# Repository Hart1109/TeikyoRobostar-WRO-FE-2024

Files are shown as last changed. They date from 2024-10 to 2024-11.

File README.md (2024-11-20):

Engineering materials「Teikyo University」
====

This repository contains engineering materials of a self-driven vehicle's model participating in the WRO Future Engineers competition in the season 2024.

---
## Member
* Ryota Kanda (Born on July 12 ,2005)
* Yusei Owa (Born on March 29 ,2006)
* Yuichi Hasuda (coach)
## Content

* `t-photos` contains 2 photos of the team (an official one and one funny photo with all team members)
* `v-photos` contains 6 photos of the vehicle (from every side, from top and bottom)
* `video` contains the video.md file with the link to a video where driving demonstration exists
* `schemes` contains one or several schematic diagrams in form of JPEG, PNG or PDF of the electromechanical components illustrating all the elements (electronic components and motors) used in the vehicle and how they connect to each other.
* `src` contains code of control software for all components which were programmed to participate in the competition
* `models` is for the files for models used by 3D printers, laser cutting machines and CNC machines to produce the vehicle elements.
* `other` is for other files which can be used to understand how to prepare the vehicle for the competition. It may include documentation how to connect to a SBC/SBM and upload files there, datasets, hardware specifications, communication protocols descriptions etc.

## Introduction
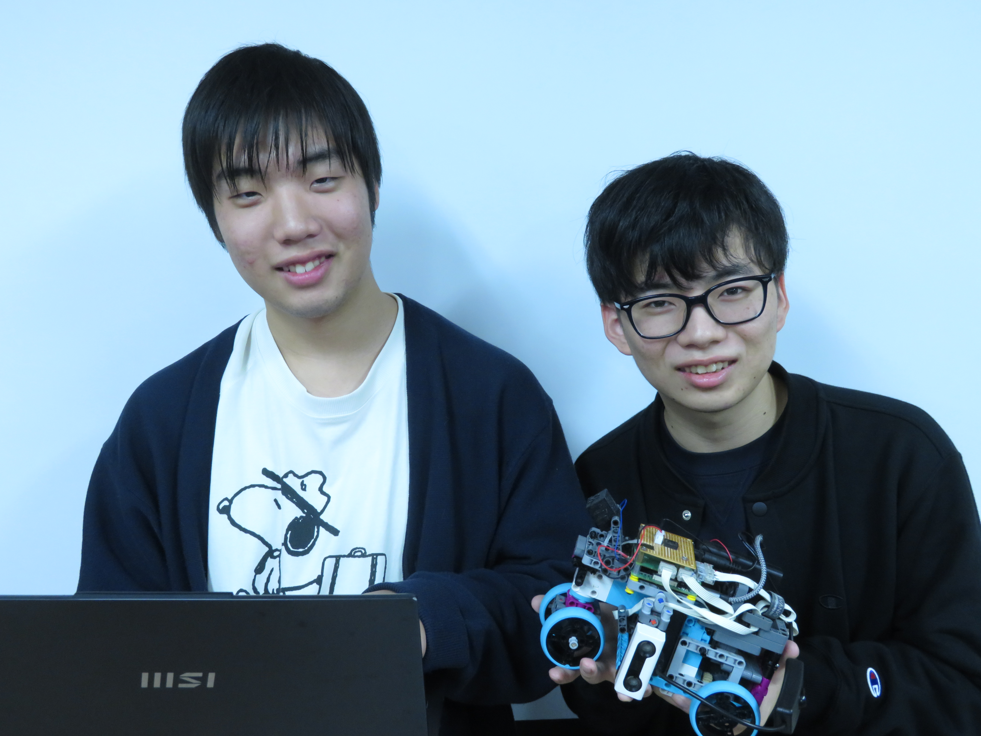
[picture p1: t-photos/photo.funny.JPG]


**Ryota Kanda:Robot design**・・・Left Side  
Ryota is a first-year student at Teikyo University and a member of the robotics club RoboLab. He is in charge of designing robots in the team and works hard practicing and designing every day. He is studying robot technology with the goal of becoming an engineer in the future. His hobbies are tea ceremony and origami.

**Yusei Owa**:Programmer・・・Right Side  
Yusei is a first-year student at Teikyo University and a member of the robotics club RoboLab. He is in charge of programming in the team. He uses the knowledge he learned in his university classes to design and improve programs. He is currently studying linux and python with the goal of becoming an engineer in the future. After school, he enjoys reading books.

---
Next, we describe the operation and programming environment of the freestanding robot.
First, download RealVNC Viewer from the following site
https://www.realvnc.com/en/connect/download/viewer/
 
 After downloading, find out the IP address of the machine and connect to it.

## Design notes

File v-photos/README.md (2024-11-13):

Vehicle's photos
====


↑Here is a picture of the back side.



↑Front side.



↑On the left.



↑Right side.



↑Bottom side.



↑Upper side.

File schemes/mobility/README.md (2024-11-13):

#  Mobility Management

## Motor Overview

### Selected motor
・SPIKE Prime L angular motor



### Specification of motor
・SPIKE Prime L angular motor
| part | performance |
| --- | --- |
| Output voltage | 5～9[V] |
| Rotation sensor  | one revolution:360count  |
| Wire  | 250mm |
| No Load |Torque: 0 Ncm <br> Speed: 175 RPM ± 15% <br> Current Consumption: 135 mA ± 15%|
| Maximum Efficiency | Torque: 8 Ncm <br> Speed: 135 RPM ± 15% <br> Current Consumption: 430 mA ± 15% |
| Stall | Torque: 25 Ncm <br> Speed: 0 RPM <br> Current Consumption: 1400 mA ± 15% |

### Reasons for choice
Easy to assemble and reassemble, making it suitable for fine-tuning of robots.In addition, the L motor for high output and high torque for both the front and rear wheels. It is a reliable and proven motor that was used by the winning team of tha WRO 2023 World Championships.

### Implementation Methods
The use of high-torque motors for the front and rear wheels is expected to shorten the competition time.

---
## Brief explanation of car body structure
The base of the robot is designed around the LEGO Education Spike Prime, and the robot is connected to a Raspberry Pi4, ultrasonic sensor, camera, cooling fan, and battery.In addition, the 3D model was used to fix the camera to prevent image distortion while the robot is running, and two ultrasonic sensors were installed on either side of the robot to keep it parallel to the wall at all times.

---
## Front wheel operation
Increasing the distance between the wheels of the vehicle has the advantage of making the steering more agile, allowing for fine angle adjustment and easier corner turning. For rough control of the wheels, the angle of the wheels is changed by turning the motor.




For a detailed explanation of the design, please click [here](https://github.com/Hart1109/TeikyoRobostar-WRO-FE-2024/blob/main/body%20information/Steering%20wheel%20assembly.pdf).

## Rear wheel operation

Differential gears are used for the rear wheel drive mechanism. The function of this component is to allow for the speed difference between the inner and outer wheels and distribute the output to both wheels, sending more power to the less loaded tire.



This mechanism enables smooth obstacle avoidance and cornering.

---

## 3Dmodels（camera mount）



This component is used to secure the Raspberry Pi Camera.

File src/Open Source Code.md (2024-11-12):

import cv2
import os
import numpy as np
import time
import threading
import RPi.GPIO as GPIO
GPIO.setmode(GPIO.BCM)
from buildhat import Motor, DistanceSensor, ColorSensor

motorBack = Motor('D')
motorFront = Motor('C')
distLeft = DistanceSensor('A', threshold_distance=100)
distRight = DistanceSensor('B', threshold_distance=100)
GPIO.setup(18, GPIO.IN, pull_up_down=GPIO.PUD_UP)

motorBack.stop()
motorFront.stop()

#Default setting
#Start speed
pw = -47
adjustment = 5

def setup():
    dist_L = distLeft.get_distance()#Stores distance to left wall
    dist_R = distRight.get_distance()#Stores distance to right wall
    motorFront.run_to_position(adjustment,blocking=False)
    print("standby")
    GPIO.wait_for_edge(18, GPIO.FALLING)
    time.sleep(0.3)
    
def setMotor():
    motorBack.set_default_speed(-pw)#Setting the motor speed of the rear wheels
    motorFront.set_default_speed(-pw)#Setting the motor speed of the front wheels

def run(pw):
    motorBack.start(pw)#Start speed setting

def stop():
    motorBack.stop()#Stops rear wheel movement
    motorFront.stop()#Stops front wheel movement

def runStraight():#Program to run horizontally against a wall
    if turnCount == 0:#When the direction is not set
        dif = dist_R - dist_L
        if (dif - firstDis < -10):
            motorFront.run_to_position(10,blocking=False)
            time.sleep(0.3)
        elif (dif - firstDis > 10):
            motorFront.run_to_position(-5,blocking=False)
            time.sleep(0.3)
    if rotation == "Left":#Counterclockwise rotation
        if dist_R < tDist - 10:
            motorFront.run_to_position(14,blocking=False)
            time.sleep(0.3)
        elif tDist - 10 <= dist_R and dist_R <= tDist + 10:
            motorFront.run_to_position(0,blocking=False)
            time.sleep(0.3)
        elif tDist + 10 < dist_R:
            motorFront.run_to_position(-6,blocking=False)
            time.sleep(0.3)
            
    if rotation == "Right":#Clockwise rotation
        if dist_L < tDist - 10:
            motorFront.run_to_position(-8,blocking=False)
            time.sleep(0.3)
        elif tDist - 10 <= dist_L and dist_L <= tDist + 10:
            motorFront.run_to_position(0,blocking=False)
            time.sleep(0.3)
        elif 250 <= dist_L:
            motorFront.run_to_position(14,blocking=False)
            time.sleep(0.3)
            
def backTurn():#Backward program
    if rotation == "Left":#Counterclockwise rotation
        motorFront.run_to_position(0,blocking=False)
        motorBack.run_for_degrees(360,-pw)
        motorFront.run_to_position(30, blocking=False)
        time.sleep(0.2)
        motorBack.run_for_degrees(50,pw)
        motorFront.run_to_position(30, blocking=False)
        time.sleep(0.2)
        motorBack.run_for_degrees(2050,pw)
        time.sleep(0.3)

    elif rotation == "Right":#Clockwise rotation
        motorFront.run_to_position(0,blocking=False)
        motorBack.run_for_degrees(360,-pw)
        motorFront.run_to_position(-30, blocking=False)
        time.sleep(0.2)
        motorBack.run_for_degrees(50,pw)
        motorFront.run_to_position(-30, blocking=False)
        time.sleep(0.2)
        motorBack.run_for_degrees(1800,pw)
        
def turn():#Turning the corner program
    if rotation == "Left":#Counterclockwise rotation
        motorFront.run_to_position(30, blocking=False)
        time.sleep(0.2)
        motorBack.run_for_degrees(50,pw)
        motorFront.run_to_position(30, blocking=False)
        time.sleep(0.2)
        motorBack.run_for_degrees(2050,pw)
        time.sleep(0.3)
        
    elif rotation == "Right":#Clockwise rotation
        motorFront.run_to_position(-30, blocking=False)
        time.sleep(0.2)
        motorBack.run_for_degrees(50,pw)
        motorFront.run_to_position(-30, blocking=False)
        time.sleep(0.2)
        motorBack.run_for_degrees(1800,pw)
      
#Enter initial values for each variable
x = 0
y = 0
finishCount = 0#Used during the finish section
allowRun = True#Determine if it is running or not.
turnCount = 0#Measure the number of times a corner is turned
rotation = ""
tDist = 0
turnWait = 0
backJudge = 200

#Mainprogram
setMotor()
setup()
while True:
    dist_L = distLeft.get_distance()#Stores distance to left wall
    dist_R = distRight.get_distance()#Stores distance to right wall
    
    if allowRun:
         run(pw)
    else:
        stop()
        break
    
    if x == 0:
        firstDis = dist_R - dist_L
        x += 1

    if rotation == "":
        runStraight()
        if dist_L < 0 or 1200 < dist_L:#If the left sensor cannot recognize the distance
            rotation = "Left"
        elif dist_R < 0 or 1200 < dist_R:#If the right sensor cannot recognize the distance
            rotation = "Right"
            
    if rotation == "Left":#Counterclockwise rotation
        if turnCount >= 12:#When you turned the corner 12 times
            if finishCount < 5:#If the count is 5 or more
                runStraight()
                finishCount += 1
            else:
                allowRun = False#If the count is less than 5
                print("stop")
                
        if (0 < dist_L and dist_L < 1200):#If the left sensor can recognize the distance
            turnWait = 0
            backJudge = dist_L
            runStraight()
            if y > 0:
                y -= 1
                
        if (dist_L < 0 or 1200 < dist_L):#If the left sensor cannot recognize the distance
            turnWait += 1
            if (y == 0) and turnWait == 2:
                print("turning")
                if backJudge < 120:#When the distance from the wall is close
                    turn()
                else:
                    backTurn()#When the distance from the wall is far
                tDist = distRight.get_distance()
                turnCount += 1
                y += 5
            else:
                runStraight()

    elif rotation == "Right":#Clockwise rotation
        if turnCount >= 12:#When you turned the corner 12 times
            if finishCount < 5:#If the count is 5 or more
                runStraight()
                finishCount += 1
            else:
                allowRun = False#If the count is less than 5
                print('stop')
                
        if (0 < dist_R and dist_R < 1200):#If the right sensor can recognize the distance
            turnWait = 0
            backJudge = dist_R
            runStraight()
            if y > 0:
                y -= 1

        if (dist_R < 0 or 1200 < dist_R):#If the right sensor cannot recognize the distance
            turnWait += 1
            if (y == 0) and turnWait == 2:
                print("turning")
                if backJudge < 120:#When the distance from the wall is close
                    turn()
                else:
                    backTurn()#When the distance from the wall is far
                tDist = distLeft.get_distance()
                turnCount += 1
                y += 5
            else:
                runStraight()
　　#Displays the value of each variable
    print(f"dL:{dist_L} dR:{dist_R} aR:{allowRun} tD:{tDist} ro:{rotation} count:{turnCount} y: {y} finish:{finishCount}")

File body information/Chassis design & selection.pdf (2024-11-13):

# Chassis design / selection

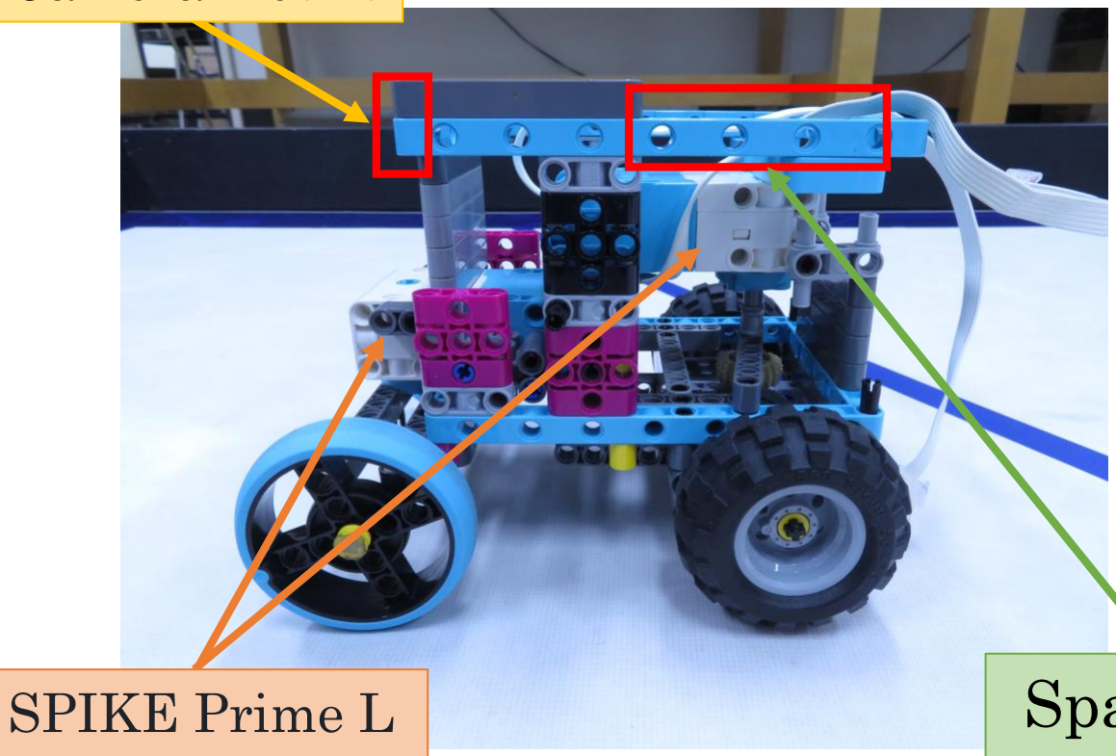
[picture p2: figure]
SPIKE Prime L

### Space for battery

Space is created at the rear of the vehicle to accommodate the mobile battery and battery box.

By creating a support with LEGO SPIKE, the parts were prevented from falling and the mounting performance was
improved.

angular motor

Camera mount

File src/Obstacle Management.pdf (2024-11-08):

# Souce code with detailed comments(1)

def setMotor():
motor.set_default_speed(100) motorS.set_default_speed(100)

def run(pw):
motor.start(pw)

def stop():
motor.stop()
motorS.stop()

## Necessary for robot

operation.forward, stop,

## etc.lograms

# Souce code with detailed comments(2)

def corner():
motorS.run_to_position(-15, blocking=False) time.sleep(0.2)
motor.run_for_degrees(300,-pw) motorS.run_to_position(15, blocking=False) time.sleep(0.2)
motor.run_for_degrees(100,pw) motorS.run_to_position(15, blocking=False) time.sleep(0.2)
motor.run_for_degrees(1000,pw)

def cornerB():
motorS.run_to_position(15, blocking=False) time.sleep(0.2)
motor.run_for_degrees(300,-pw) motorS.run_to_position(-15, blocking=False) time.sleep(0.2)
motor.run_for_degrees(100,pw) motorS.run_to_position(-15, blocking=False) time.sleep(0.2)
motor.run_for_degrees(1000,pw)

## 90-degree bend along an interior wallProgram for

# Souce code with detailed comments(3)

def correct_value(n):
if n < 150:
return 150
elif n > 450:
return 450
else:

setMotor()
cornerOn=False
x=0
segment_p = 0
dis = -1
count = 0
countB = 0
countC = 0
non = 0
CC = 0
CCC = 0

## Program to limit ultrasonic sensor values to a minimum of 150 and a maximum of 450

## Set initial values of variables necessary for executing the main program

while True:
if x == 0:
stop()
print('setup')
GPIO.wait_for_edge(18, GPIO.FALLING)

if rotation == “”:
runStraight()
if dist_L < 0 or 1200 < dist_L: rotation = “Left”
elif dist_R < 0 or 1200 < dist_R: rotation = “Right”

if shukai ==1:
dis_p = dist.get_distance()
else:
dis_p = distB.get_distance()

motorS.run_to_position(0, blocking=False) time.sleep(0.5)
run(pw)
x = 1

if count >=12:
CCC += 1
print (CCC)
if CCC == 100 :
stop()
break

## Main program Program to start the robot with a switch A program that counts the number of bends and stops the robot above a certain value

# Souce code with detailed comments(4)

# Souce code with detailed comments(5)

if shukai ==1:
dis = dist.get_distance()
else:
dis = distB.get_distance()

countB += 1
if dis == -1 or dis >1100 :
non += 1

if non >= 10 and countB >=180 or non > 15: if non > 10:
if shukai == 1:
cornerC()
else:
cornerD()
else:
if shukai == 1:
corner()
else:
cornerB()
if countB >= 120 or count == 0 and countB <= 119: count +=1

countC = 0
countB = 0
run(pw)

## Program measures distance to wall and moves forward while maintaining distance.When the distance becomes much larger than the measured value Or when it becomes unmeasurable,The

program turns 90 degrees.

# Souce code with detailed comments(6)

count +=1

countC = 0
countB = 0
run(pw)

while not 0 < dis < 340 and not countC > 60: if shukai == 1:
dis = dist.get_distance()
print(dis)
countC += 1
print(countC)
else:
dis = distB.get_distance() print(dis)
countC += 1
print(countC)

countC = 0
countD = 0

motorS.run_to_position(0, blocking=False) motor.run_for_degrees(100,pw)

## If the distance between the robot and the inner wall is too far after a 90-degree turn, program the robot to turn until a certain distance is

reached.

# Souce code with detailed comments(7)

if dis == -1:
if shukai == 1:
segment = 10
else:
segment = -10

elif dis <= 200:
if shukai == 1:
segment = -10
else:
segment = 10

elif dis <= 100:
if shukai == 1:
segment = -15
else:
segment = 15

## Program to change steering depending on distance from wall

elif dis >1000:
segment = 0

elif -10 <= dis_p - dis <= 25: segment = 0

elif 25 < dis_p - dis:
if shukai == 1:
segment = -5
else:
segment = 5

elif dis_p - dis < 30:
if shukai == 1:
segment = 10
else:
segment = -10

# Pseudo code

## Determine the color of the obstacle with the greatest width in the

camera's view.
↓

## When the width of the obstacle reaches the standard value, start

evasive action.
↓

## If the obstacle is red, avoid it to the right. If the obstacle is green, avoid it

to the left.

## Obstacle Challenge

# Frow diagrams

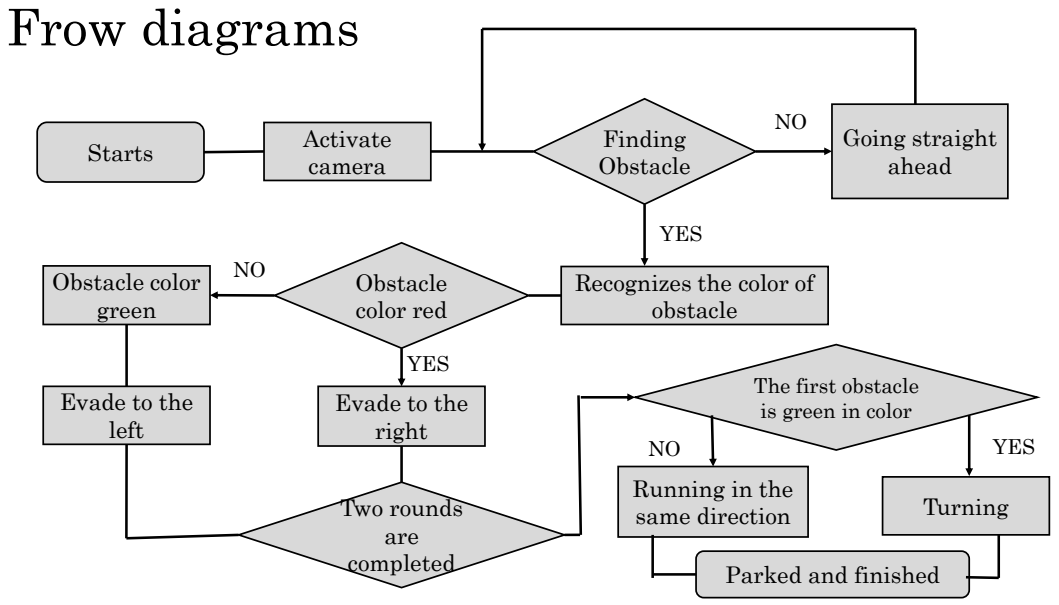
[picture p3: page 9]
Starts; Activate camera; Finding Obstacle; Going straight ahead; obstacle; Obstacle color red; Obstacle color green; Two rounds are completed; Turning; YES

Recognizes the color of

The first obstacle
is green in color

Evade to the
left

right

Running in the
same direction

Parked and finished

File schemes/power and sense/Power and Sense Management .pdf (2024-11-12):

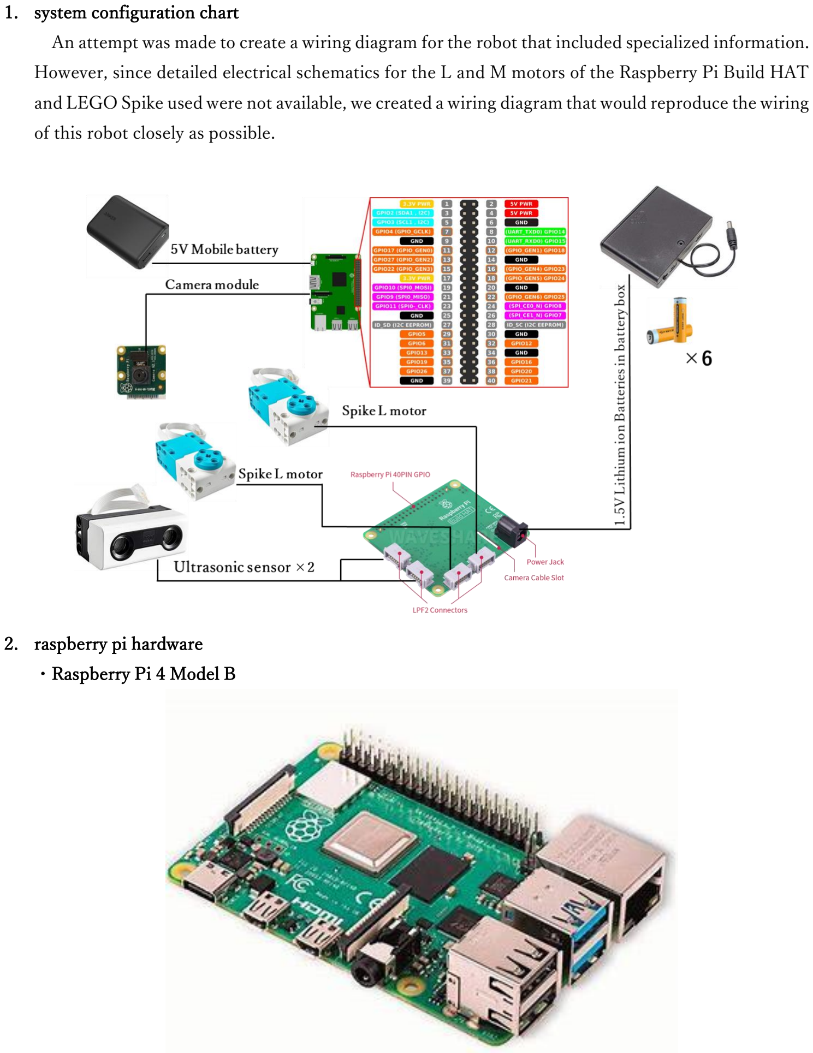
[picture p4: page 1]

1. system configuration chart
An attempt was made to create a wiring diagram for the robot that included specialized information. However, since detailed electrical schematics for the L and M motors of the Raspberry Pi Build HAT and LEGO Spike used were not available, we created a wiring diagram that would reproduce the wiring of this robot closely as possible.
2. raspberry pi hardware
・Raspberry Pi 4 Model B

(1) Product Information
part | Description
Processor | Broadcom BCM2711 Quad-Core Cortex-A72 (ARM v8) 64-bit SoC @ 1.5GHz
Memory | 8GB
Connectivity | 2.4GHz and 5.0GHz, IEEE 802.11b / g / n / ac wireless LAN, Bluetooth 5.0, BLE Gigabit Ethernet 2 x USB 3.0 ports 2 x USB 2.0 ports.
GPIO | Standard 40-pin GPIO header
Video sound | 2 x micro HDMI ports (supports up to 4Kp60) 2 lane MIPI DSI display port 2 lane MIPI CSI camera port 4-pole stereo audio and composite video port
Multimedia | H.265 (4Kp60 decoding); H.264 (1080p60 decoding, 1080p30 encoding) H.264 (1080p60 decode, 1080p30 encode) OpenGL ES, 3.0 graphics
SD card | Micro SD card slot for loading operating system and data storage
Input power | 5V DC (min. 3A1) via USB-C connector 5V DC via GPIO header (min. 3A1) Power over Ethernet (PoE) support (PoE HAT required separately)
(2) Reasons for choosing the Raspberry Pi 4 Model B
Lightweight and fast, it is the easiest single-board computer to use. It is highly flexible and can use a variety of sensors. It is also the most widely used single board computer by many people and is widely used in the field of electronic engineering, providing a wealth of information necessary for development.
(3) How to use the Raspberry Pi 4 Model B
The Raspberry Pi 4 is a small single board computer. It processes and analyzes images acquired from cameras in real time. The language used is Python and the opencv library is used for image processing.

・Raspberry Pi Build HAT

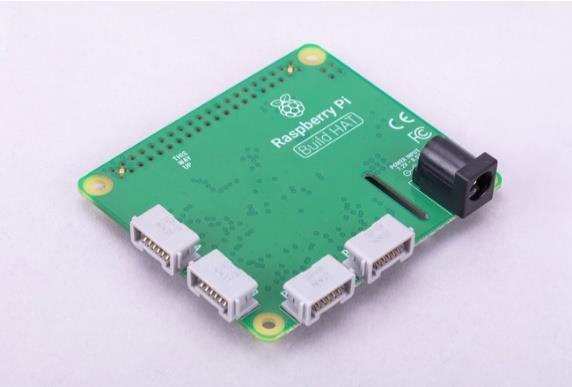
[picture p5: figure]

（１） Product Information
This product was used
https://www.switch-science.com/products/7565

（２） Reasons for choosing the Raspberry Pi Build HAT
The Raspberry Pi Build HAT can control up to four LEGO® Technic motors and sensors from a Raspberry Pi 4. The LEGO® Technic devices can be controlled by the easy-to-use Python libraries included in the LEGO® Education SPIKE Prime and SPIKE Prime Extension Sets.

（３） How to use the Raspberry Pi Build HAT
The Raspberry Pi Build HAT is not only used as an expansion port for angular motors and ultrasonic sensors, but also has the ability to step down a 9V power supply to 5V with its built-in switching regulator.
3. used battery
3-1 5V mobile battery

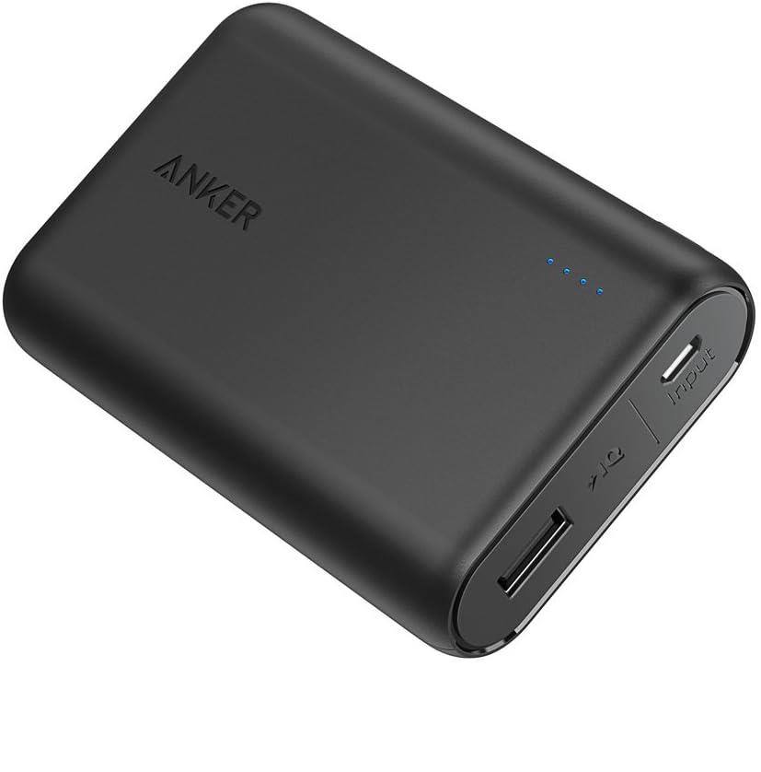
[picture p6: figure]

(1) Product Information
part | Description
capability | 10000mAh
manufacturer | Anker
Model number of the product | A1263
output | 5V = 2.4A
input | 5V = 2A
size | 92 x 60 x 22mm
weight | 180g
(2) Reason for selecting this part

To provide a stable power supply to the Raspberry Pi4. and 9V battery box is also used, which also

serves as a sub-battery. This allows the autonomous robot to operate for extended periods of time.

(3) How this was used
It is used to supply power to the Raspberry Pi4. This power is further supplied to the hub via a cable.

3-2 1.5V lithium ion Batteries in battery box

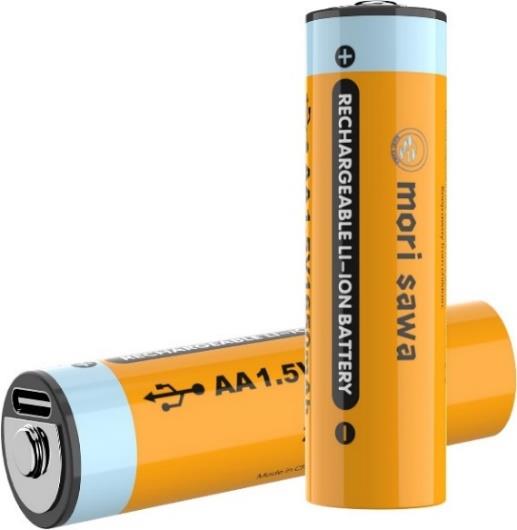
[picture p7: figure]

(1) Product Information
part | Description
type name | AA Li-ion USB
brand name | MORI SAWA
Battery types | lithium ion
Rated voltage/battery energy | 1.5V/2500mWh
Charging voltage/charging current | 5V/380mA
Battery weight | 34g
size | 15 x 15 x 50 mm
Charging time | 60 minutes (rapid: 40 minutes)
(2) Reason for selecting this part
It has a USB-C charging port and can be recharged to provide a stable power supply. It can also be recharged for multiple uses, which is good for the environment.
(3) How this was used
Six batteries are placed in a battery box, outputting 9V.

3-3 9V battery box

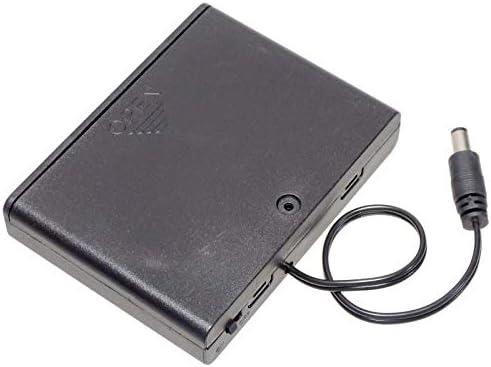
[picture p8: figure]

(1) Product Information
part | Description
style | 9V battery box
Manufacturer | KAUMO
size | 96 × 75 × 19 mm
weight | 55g
(2) Reason for selecting this part
To provide a stable power supply to the Raspberry Pi Build HAT.
(3) How this was used
Provides power to the Raspberry Pi Build HAT.
4. camera module

・Product Information

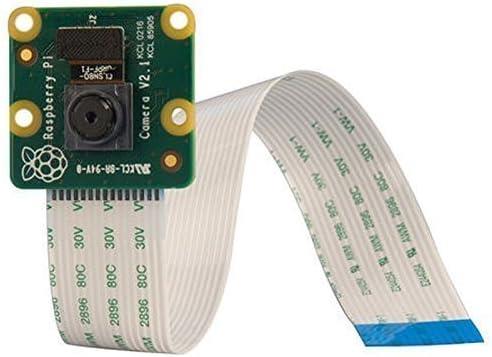
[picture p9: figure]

part | Description
Product Composition | Raspberry Pi Camera V2
Brands | Raspberry Pi
Video Pixels | 480p.x2160p, 1080p
Image Capture Speed | 60fps
model number | Raspberry Pi 3B
screen size | 2inches

・ Reasons for selecting this part
This camera module was developed specifically for the Raspberry Pi, so it is optimized for the Raspberry Pi 4 and can capture and record high quality images.

・How this was used.
Using a 15cm flexible flat cable, connect the module slot to the camera serial interface port on the Raspberry Pi. It is also used to determine the course environment in competitions.
5. flexible flat cable

・How this was used

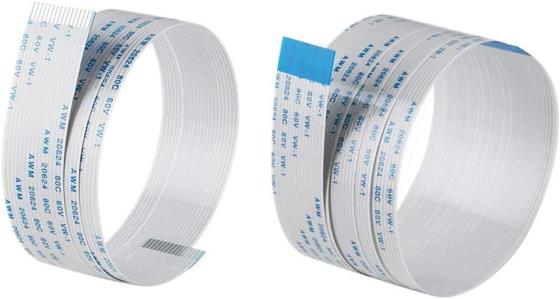
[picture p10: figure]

This cable is integrated with the camera module and is used to connect the Raspberry Pi. The cable is plugged into the connection on the Raspberry Pi side for connection.

・connector

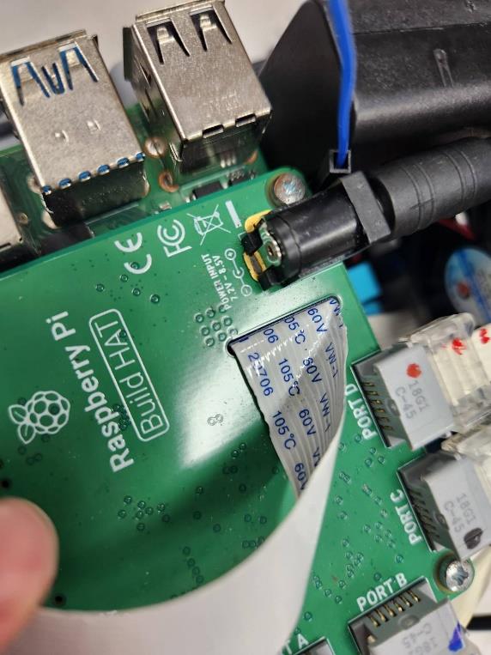
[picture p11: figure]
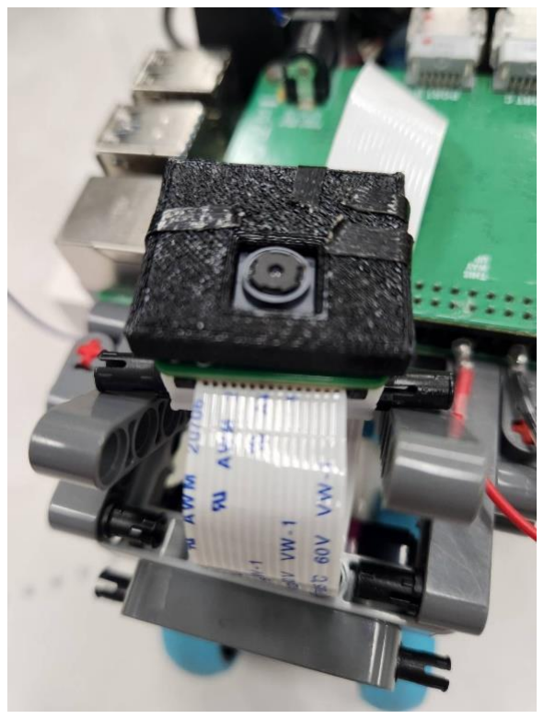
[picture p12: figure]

6. cooling fan for RaspberryPi4
(1) Product Information

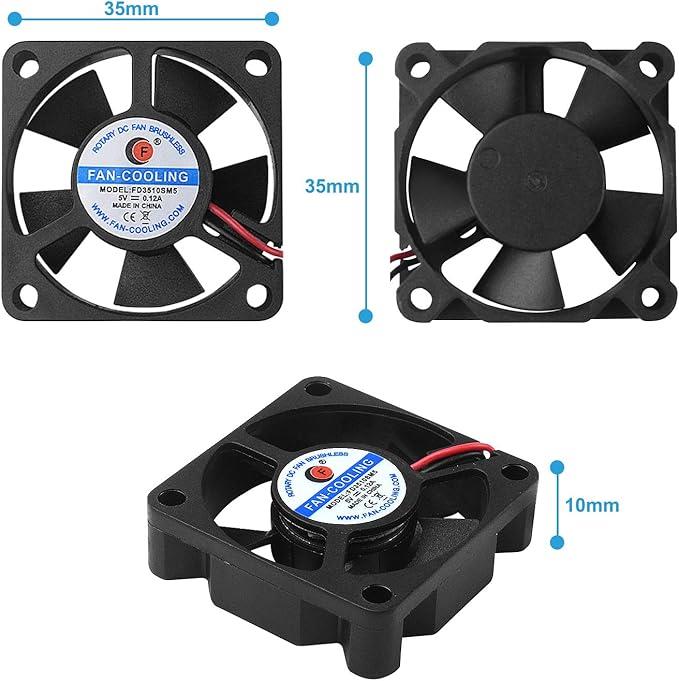
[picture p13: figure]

part | Description
Manufacture | Smraza
Voltage/current | 5V/0.12A
(2) Reason for selecting this part
The main cause of heat generation is higher performance and higher clock frequencies: in the Raspberry Pi 4 Model B, the temperature around the SoC and PMIC rises when the temperature exceeds 80°C, thermal throttling functions to protect the SoC by gradually lowering the clock frequency to 600 MHz to protect the SoC. Once thermal throttling is functioning, operation becomes unstable. Therefore, cooling fans are used to lower the temperature around the SoC and PMIC.
(3) How this was used.
Used to cool Raspberry Pi4.

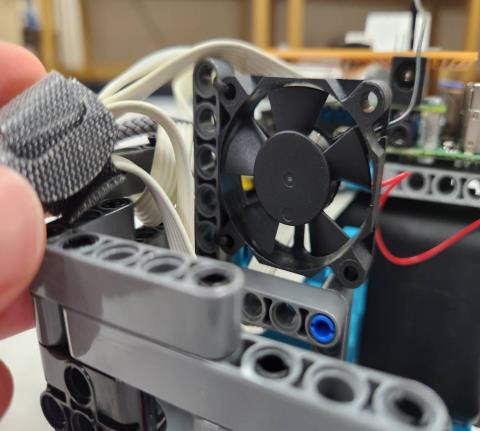
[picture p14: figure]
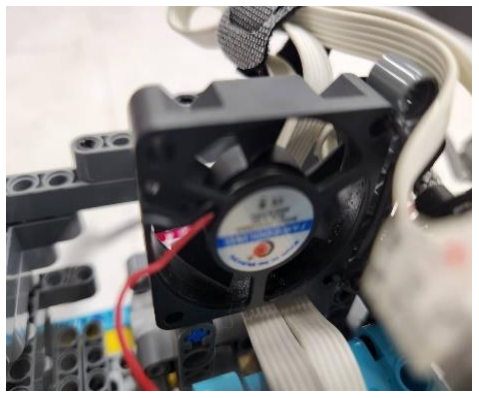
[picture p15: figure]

7. heatsink for RaspberryPi4
(1) Reason for selecting this part

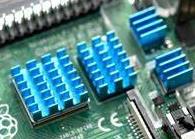
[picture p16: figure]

To prevent excessive heating and stabilize Raspberry Pi4 functionality.

(2) How this was used.
Attaching a heat sink to the SoC increases the surface area that is exposed to cooling fan airflow, resulting in more efficient cooling.
8. Cable used
・USB type A to USB type C connector
(1) Reason for selecting this part

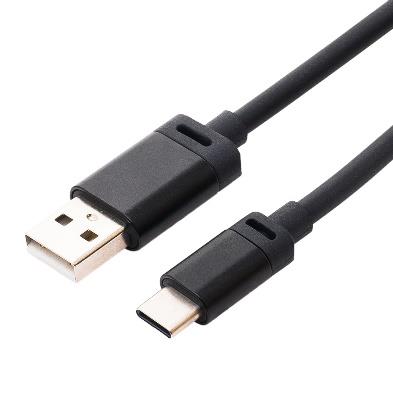
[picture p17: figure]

Used to supply power from a mobile battery to a Raspberry Pi4.

(2) How this was used
It is connected between the mobile battery and the Raspberry Pi4 and supplies power from the mobile battery to the Raspberry Pi4.
(3) Connections

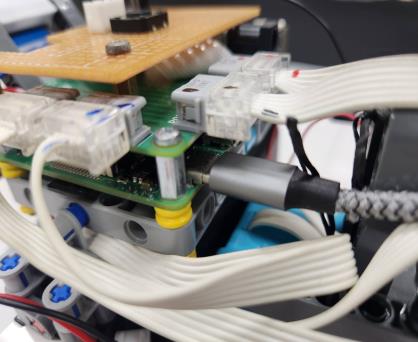
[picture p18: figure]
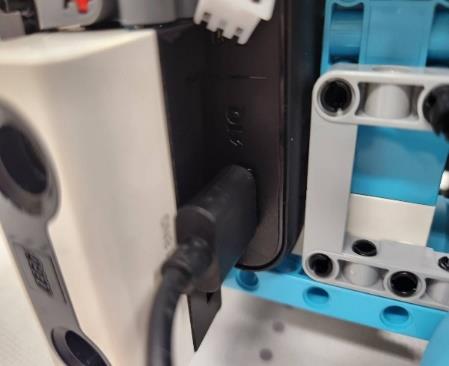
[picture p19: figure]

9. Motor
spike L motor

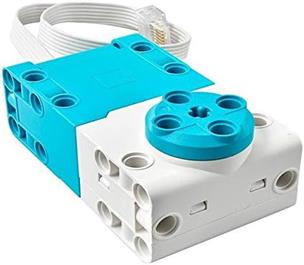
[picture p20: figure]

×2

(1) How this was used.
Click here for details
https://github.com/Hart1109/TeikyoRobostar-WRO-FE2024/tree/main/schemes/mobility
10. ultrasonic sensor
(1) How this was used.

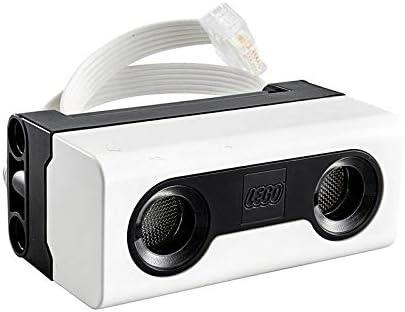
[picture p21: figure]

It was connected to a port on the Raspberry Pi Build HAT and used to measure the distance between the inner wall and the expected distance and between the outer wall and the robot.

(2) connector

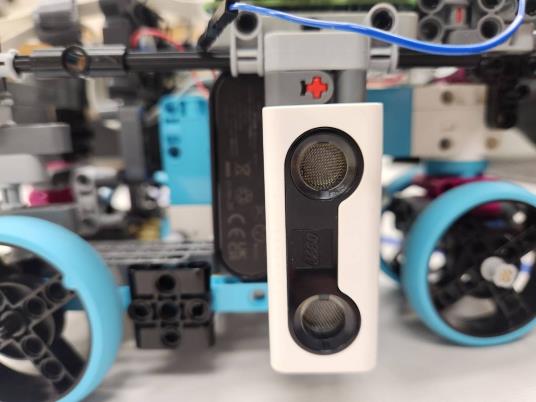
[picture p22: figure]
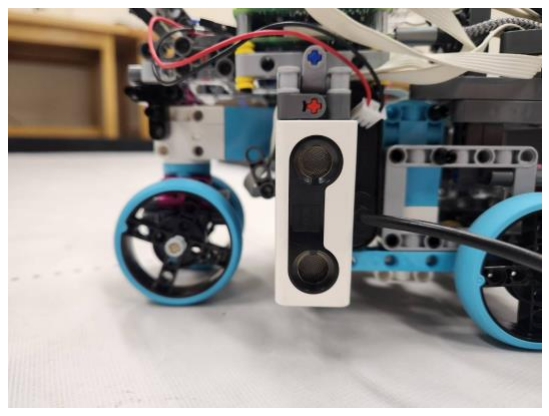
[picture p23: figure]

11. description of power supply method
Power to the Raspberry Pi 4 was supplied from a mobile battery. The procedure is as follows.
(1) Prepare mobile battery
↓
(2) Connect the mobile battery to the Raspberry Pi 4 ↓
(3) Supply power to the Raspberry Pi 4
12. description of power supply method
Power to the Raspberry Pi Build HAT was supplied from the 9V battery box. The procedure is as follows

(1)Prepare 9 V battery box.
↓
(2) Connect the 9 V battery box to the Raspberry Pi Build HAT ↓
(3) Supply power to the Raspberry Pi Build HAT
↓
(4)Prepare the 9V battery box and use six 1.5V AA batteries in the battery box to power the Raspberry Pi Build HAT.
13. Power consumption of autonomous robot
The Raspberry Pi Build HAT is powered by 9V, and the built-in switching regulator steps down the 9V to 5V to feed the Raspberry Pi 4. The autonomous robot consumes an average of 2.7W when stopped. When the camera, ultrasonic sensor, and motors are running, the average power consumption is 7.65W.

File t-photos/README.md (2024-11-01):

Team's photos
====


This is a funny phto.

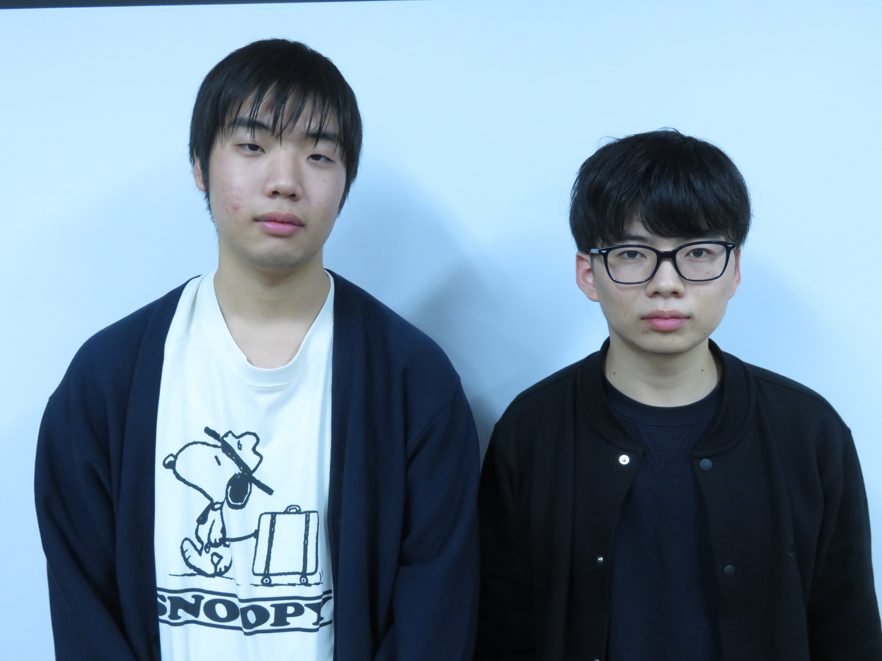
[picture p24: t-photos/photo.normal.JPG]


this is a normal photo.

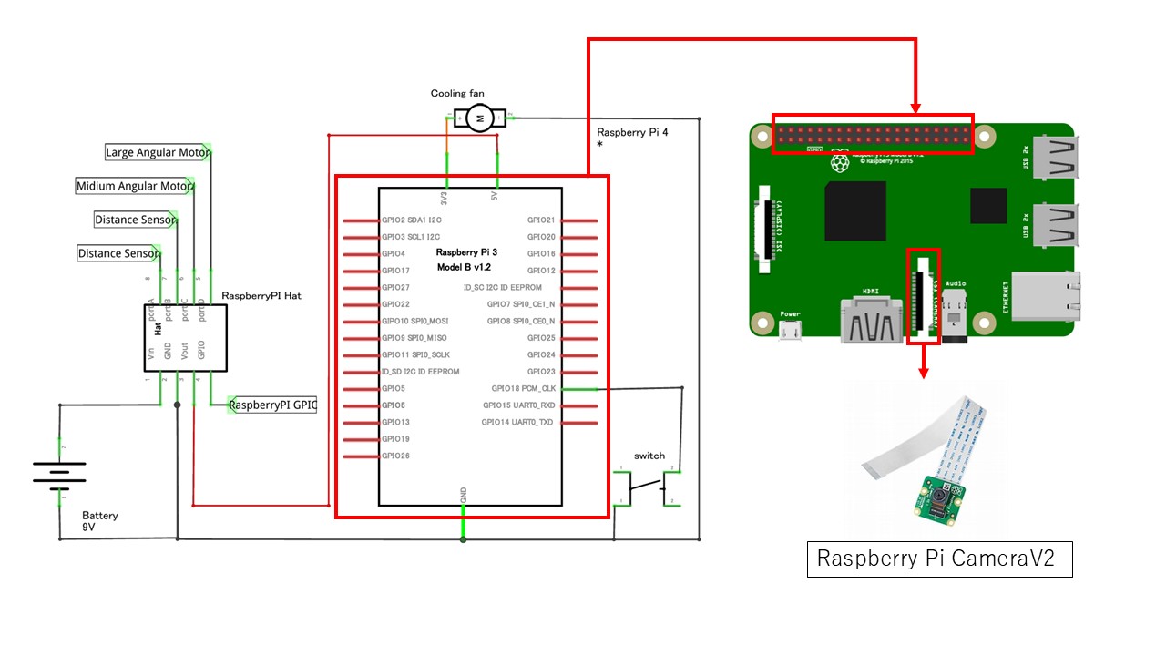
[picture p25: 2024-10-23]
schemes/power and sense/images/schematic.jpg

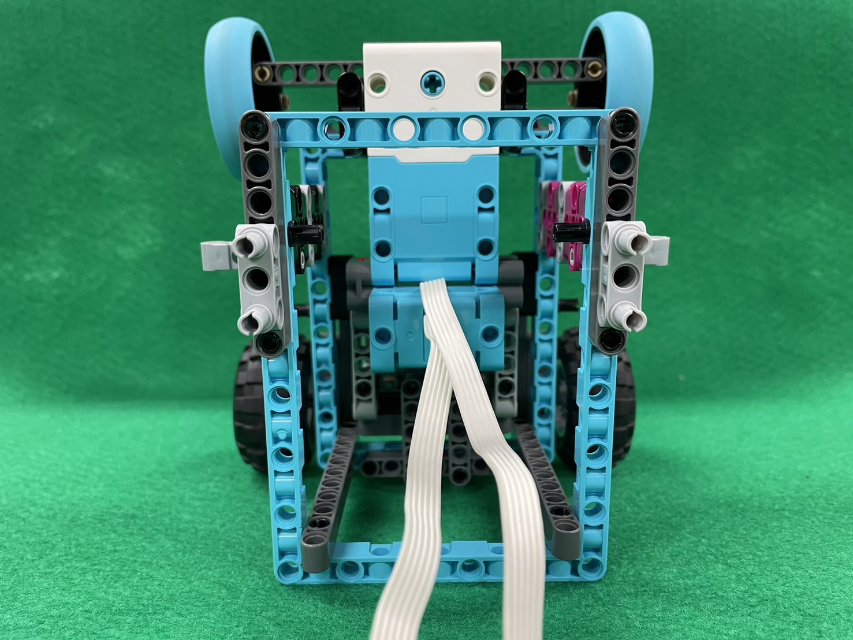
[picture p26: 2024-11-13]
body information/Chassis_01.JPG

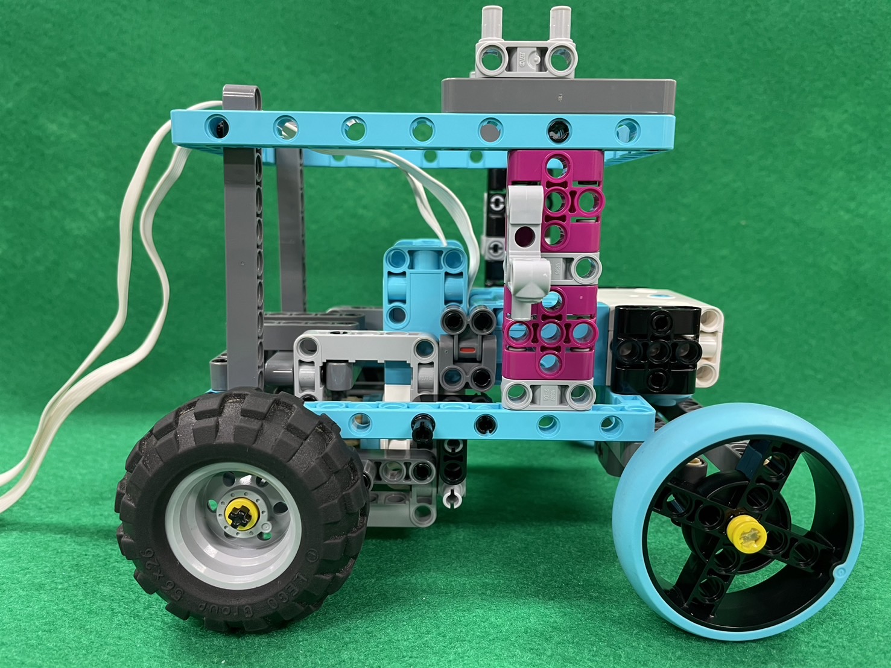
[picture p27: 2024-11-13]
body information/Chassis_03.JPG

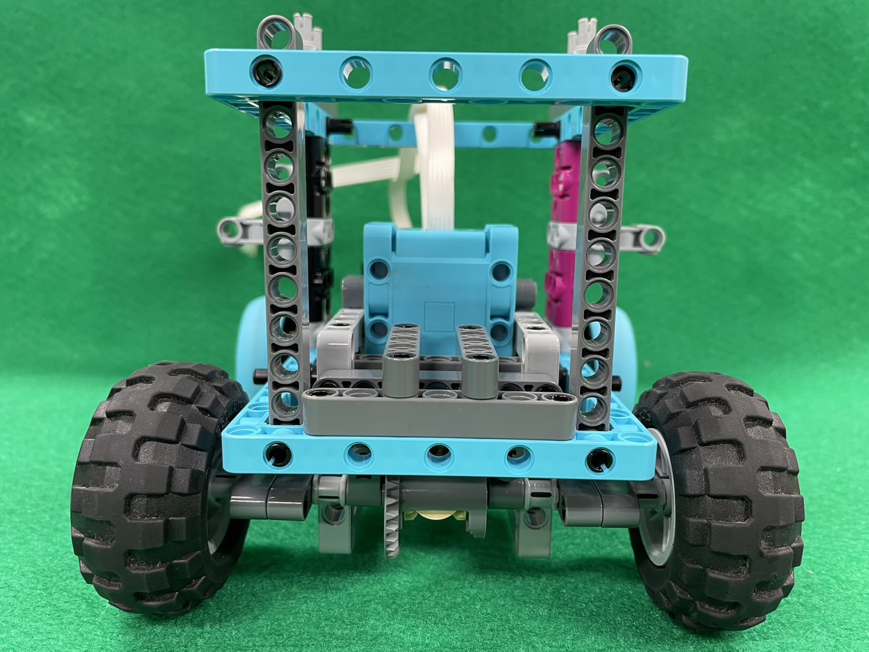
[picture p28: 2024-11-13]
body information/Chassis_05.JPG

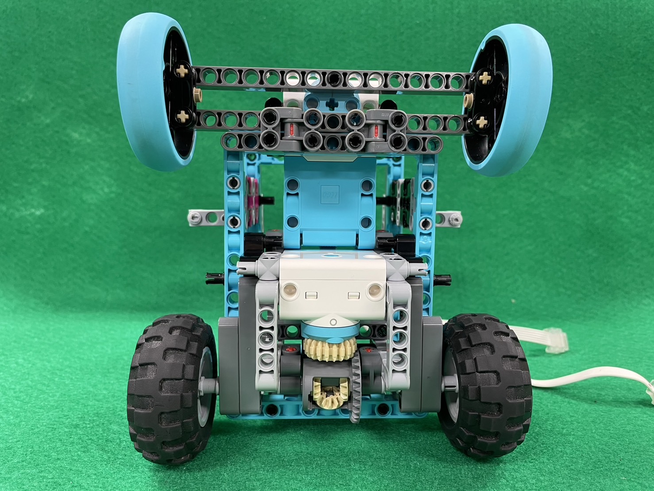
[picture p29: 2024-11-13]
body information/Chassis_06.JPG

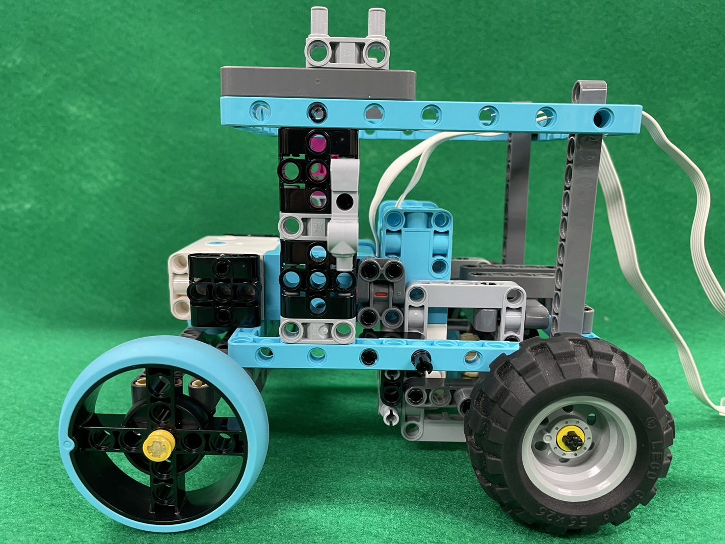
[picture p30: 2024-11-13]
body information/Chassis_02.JPG

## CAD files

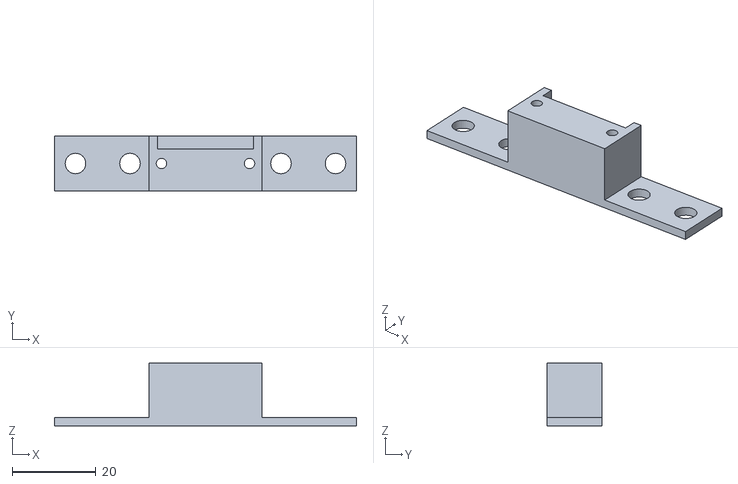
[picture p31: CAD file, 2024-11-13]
body information/3Dmodels.stl
72.0 x 13.0 x 15.0

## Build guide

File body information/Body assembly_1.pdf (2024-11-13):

How to assemble the car body

1.Differential gear and rear wheel section

### 2. Upper part of the body

3.Fixing part of Raspberry Pi and camera

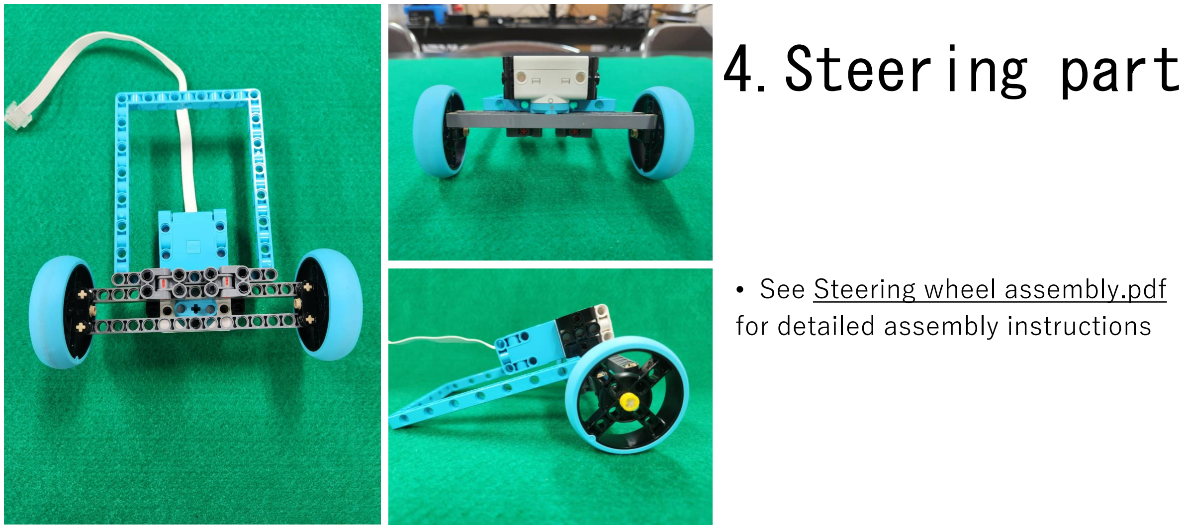
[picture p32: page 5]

4.Steering part

- See Steering wheel assembly.pdf for detailed assembly instructions

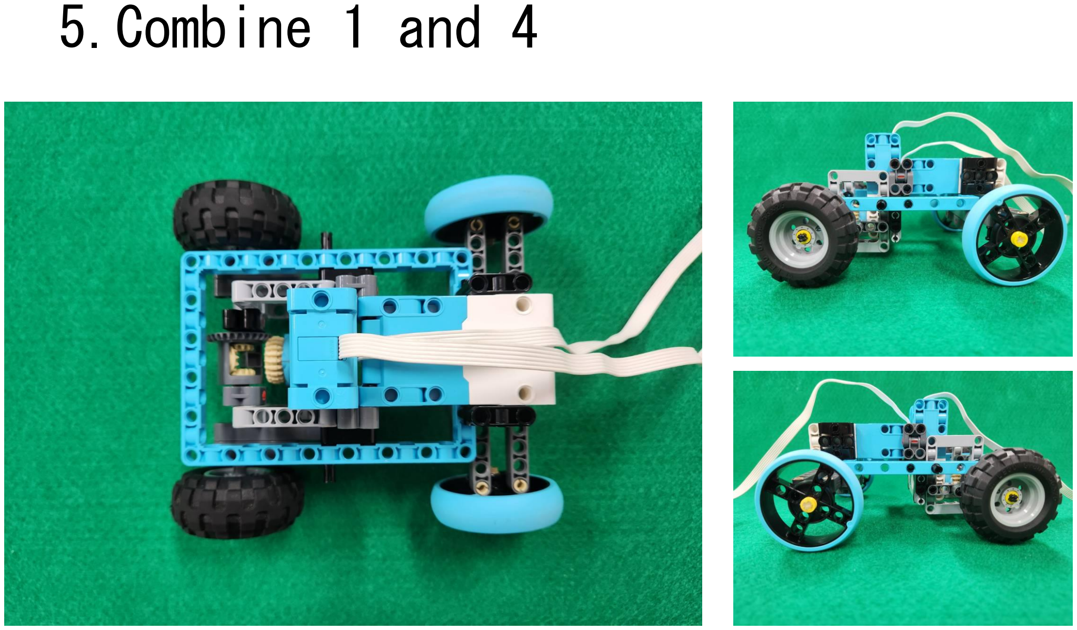
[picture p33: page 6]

5.Combine 1 and 4

6.In addition, a differential gear guard is combined.

### 7.Combine 2 and 3

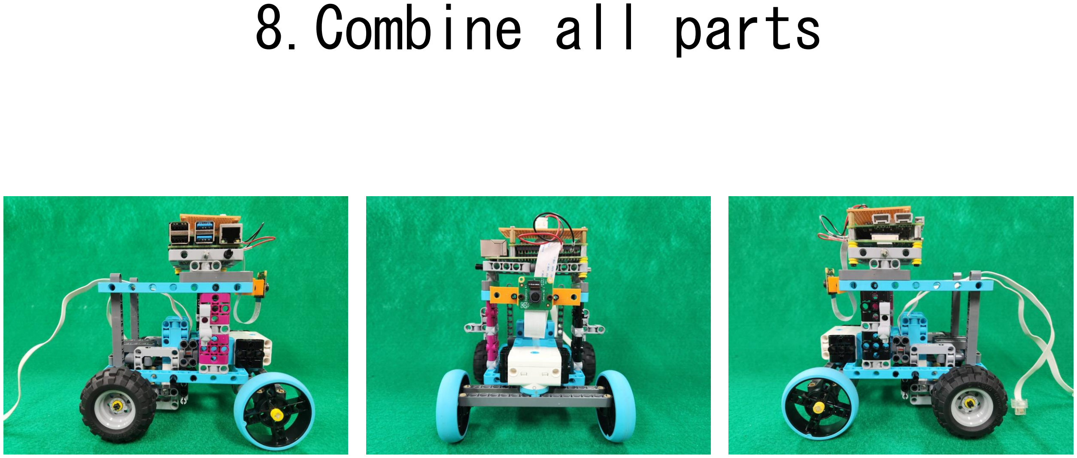
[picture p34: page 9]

### 8.Combine all parts

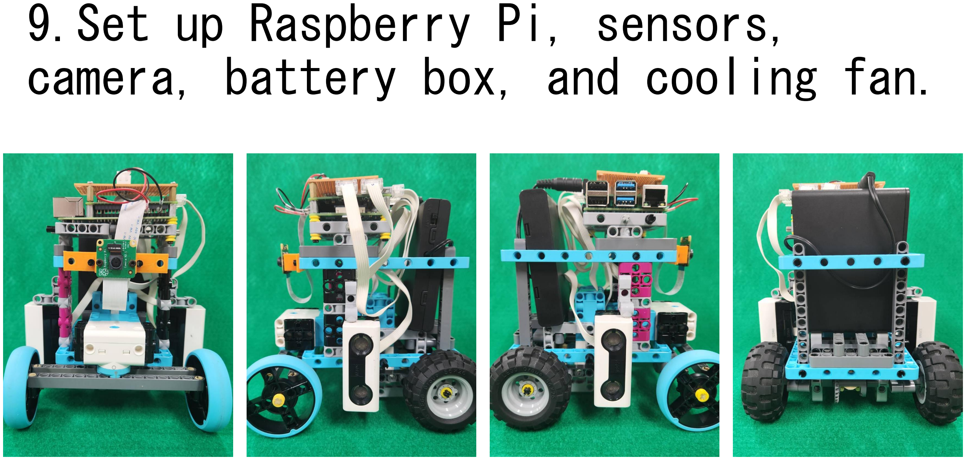
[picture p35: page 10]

9.Set up Raspberry Pi, sensors, camera, battery box, and cooling fan.

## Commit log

2024-10-25 Create Schematic
2024-10-25 Create power and sense
